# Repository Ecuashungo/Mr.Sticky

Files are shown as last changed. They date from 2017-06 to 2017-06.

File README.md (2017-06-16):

# Mr.Sticky
Mr.Sticky is a robot that has been designed and built in the framework of the STI interdisciplinary robotics competition at EPFL. The working principle of this bottle collecting robot is a sticky conveyor belt that turns around the whole chassis which is used to grab, store and release the bottles.
The data acquisition and its processing is done on board. The bottle detection uses a classifier trained by a Haar cascade using the OpenCV library. The localization of the robot is calculated through a Kalman filter which uses data from encoders and a self-built triangulation system. The latter detects four LED beacons using a camera with a parabolic lens resulting in a panoramic 360 degree view.
This project allowed us to gain experience in time and budget management as well as practical experience such as mechanical design, PCB manufacturing and software programming. 

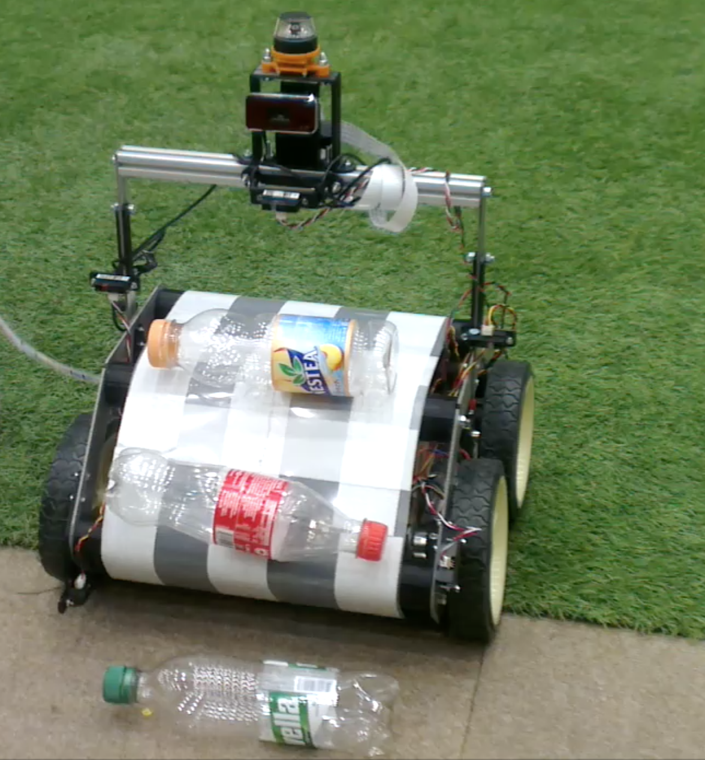
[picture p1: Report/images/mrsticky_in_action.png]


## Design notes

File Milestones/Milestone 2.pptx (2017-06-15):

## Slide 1

STI – robot competition

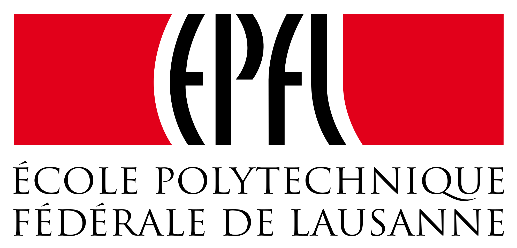
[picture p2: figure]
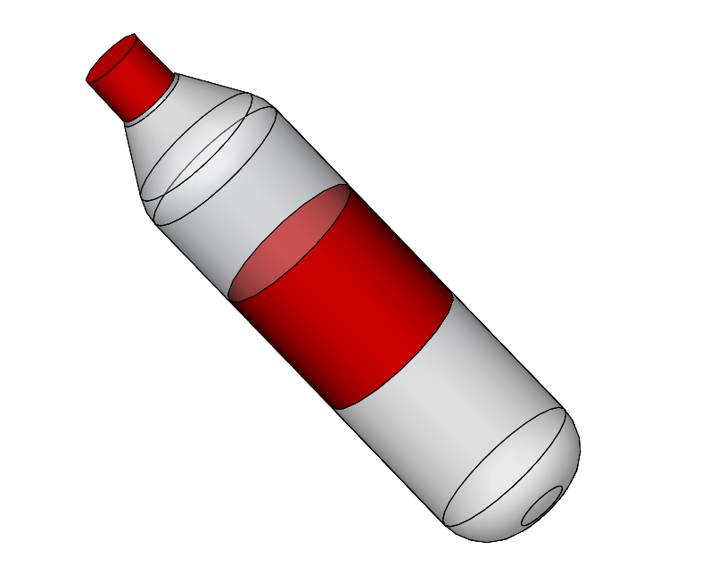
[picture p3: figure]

TEAM 3
Milestone number 2

Claudio Fritsche (GM)
Roman Oechslin (MT)
Héloïse Boross (MT)

20th March 2017

## Functional Analysis

Mechanical Functions | Other Functions
Locomotion | Bottle Detection
Grabbing Mechanism | Obstacle Avoidance
Release Mechanism | Localisation and Navigation
Storage | Time Control
Energy Supply

Research Concept Implementation Risk management

2

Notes: Claudio

## Brainstorming

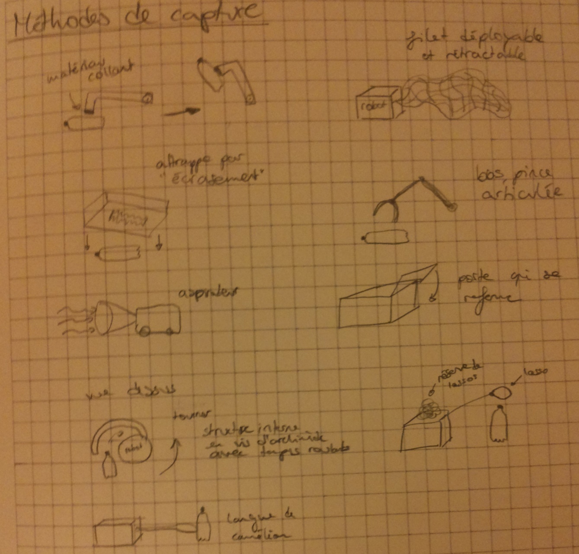
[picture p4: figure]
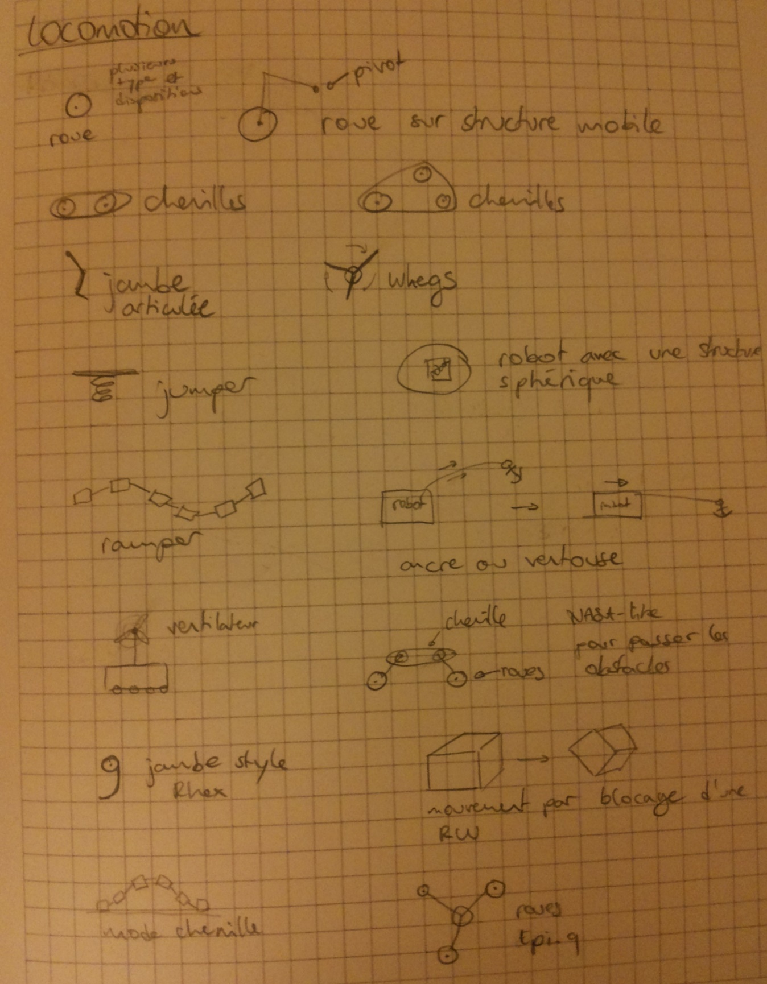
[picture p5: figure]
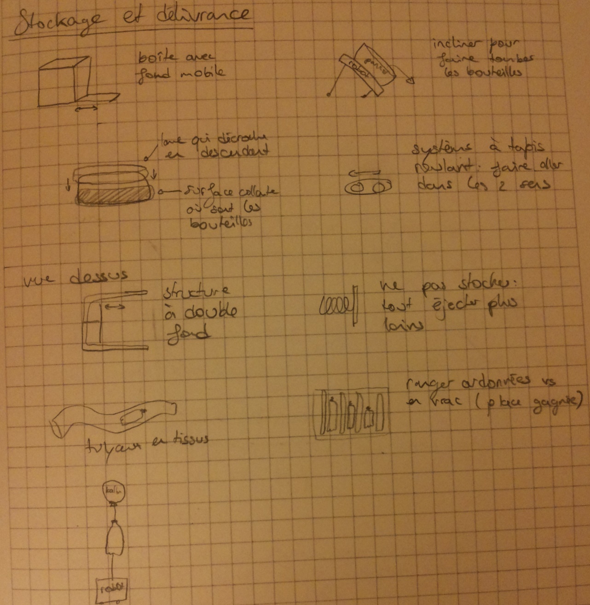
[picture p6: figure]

Research Concept Implementation Risk management

3

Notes: Héloïse

## Robot Design

Grabbing mechanism: sticky conveyor belt

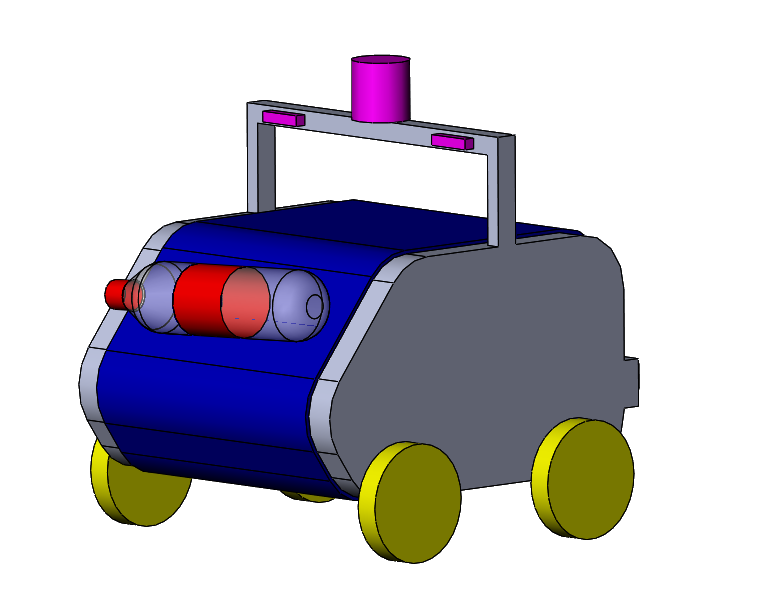
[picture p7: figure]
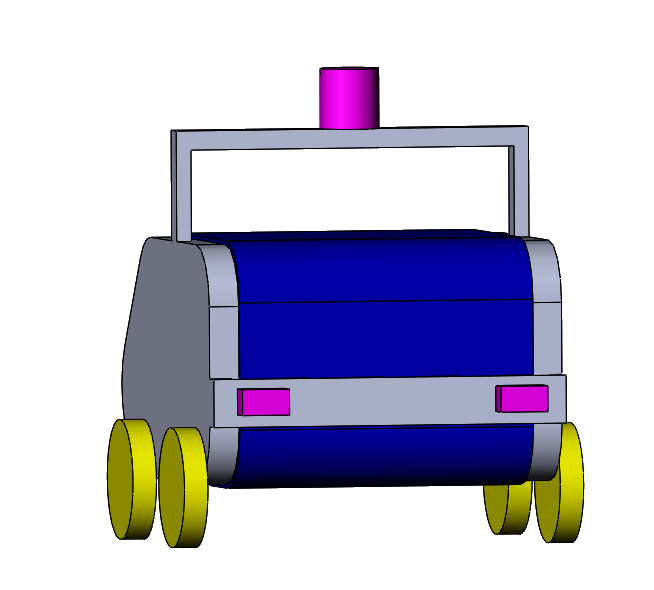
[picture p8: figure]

Bottle releasing mechanism

Navigation and obstacle detection sensors

Calibration sensors

Electronic and battery storage

Locomotion system

Bottle releasing sensor

Research Concept Implementation Risk management

4

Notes: Héloïse
locomotion, grabbing, release —> good explanation
innovative

## Robot Design

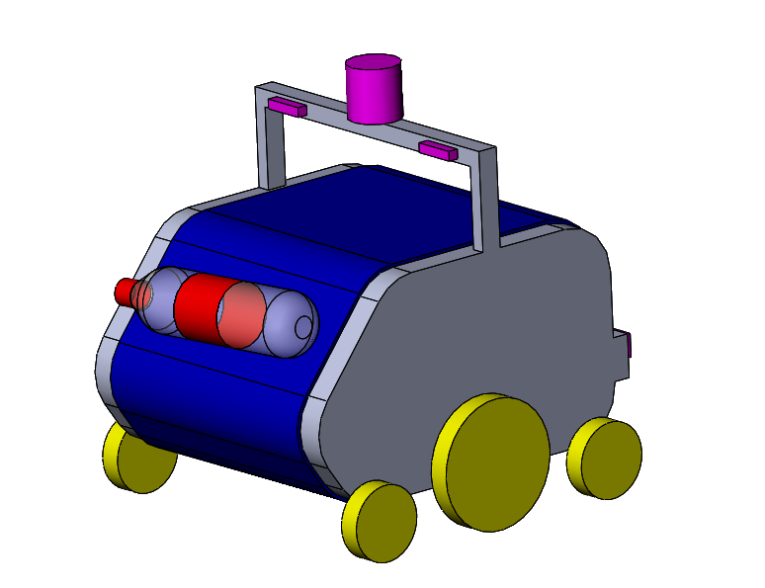
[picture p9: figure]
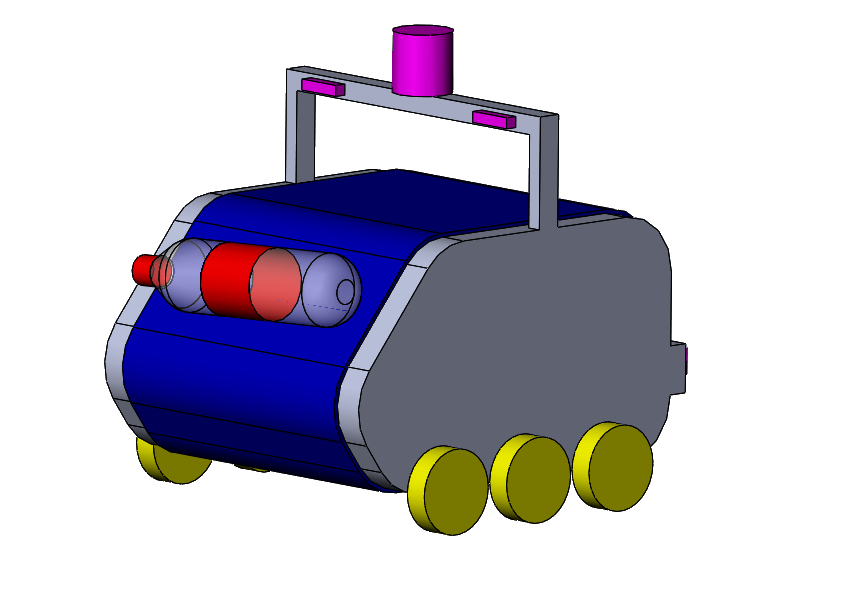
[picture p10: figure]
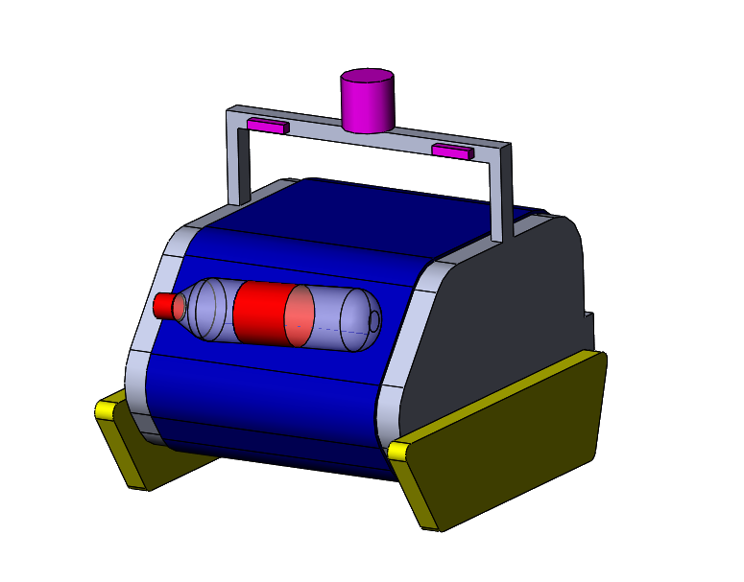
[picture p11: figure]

Research Concept Implementation Risk management

5

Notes: Héloïse
locomotion, grabbing, release —> good explanation

## Parts List

Function | Parts
Locomotion | Chassis | Motors (4x) | Controller (Arduino)
Grab and Release | Conveyor Belt | Sticky Surface | Motor
| Barrier | Light Barrier Sensor | Encoder
Navigation | Encoders (2x) | Camera | Spherical Mirror
| Bumpers (2x)
Bottle Detection | Camera | Raspberry Pi
Obstacle Avoidance | IR-Sensors
Energy Supply | Battery

Research Concept Implementation Risk management

6

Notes: Claudio

Partslist:
Locomotion:
Chassis, Wheels (4x), Motors (4x), Controller (Arduino)

Grabbing + Release:
Conveyor Belt + Sticky surface, 1 Motor (+encoder?), Barrier, Light barrier sensor

Navigation:
encoders (2x or 4x?), camera, spherical mirror

Bottle detection:
Camera, Raspberry Pi with opencv and ROS

Obstacle avoidance:
IR-sensors,

## Open CV

Why OpenCV?
- It’s an open source computer vision library
- Only one sensor (camera) for bottle detection in real time

What? | How? | To Do
Bottle Detection | Haar Cascade | Build Haar Classifier
Navigation | Triangulation with LED’s | Color detection, angle determination
Obstacle Avoidance | Haar Cascade | Build Haar Classifier

Research Concept Implementation Risk management

7

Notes: Claudio

## Navigation

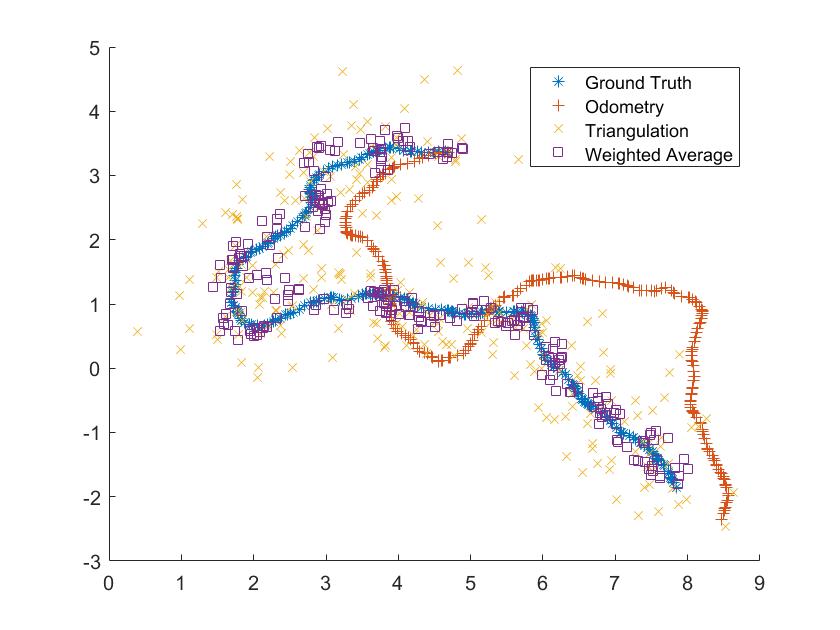
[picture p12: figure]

SLAM / Kalman filter
- Odometry (drift)
- Triangulation (noisy)
- Monocular vision

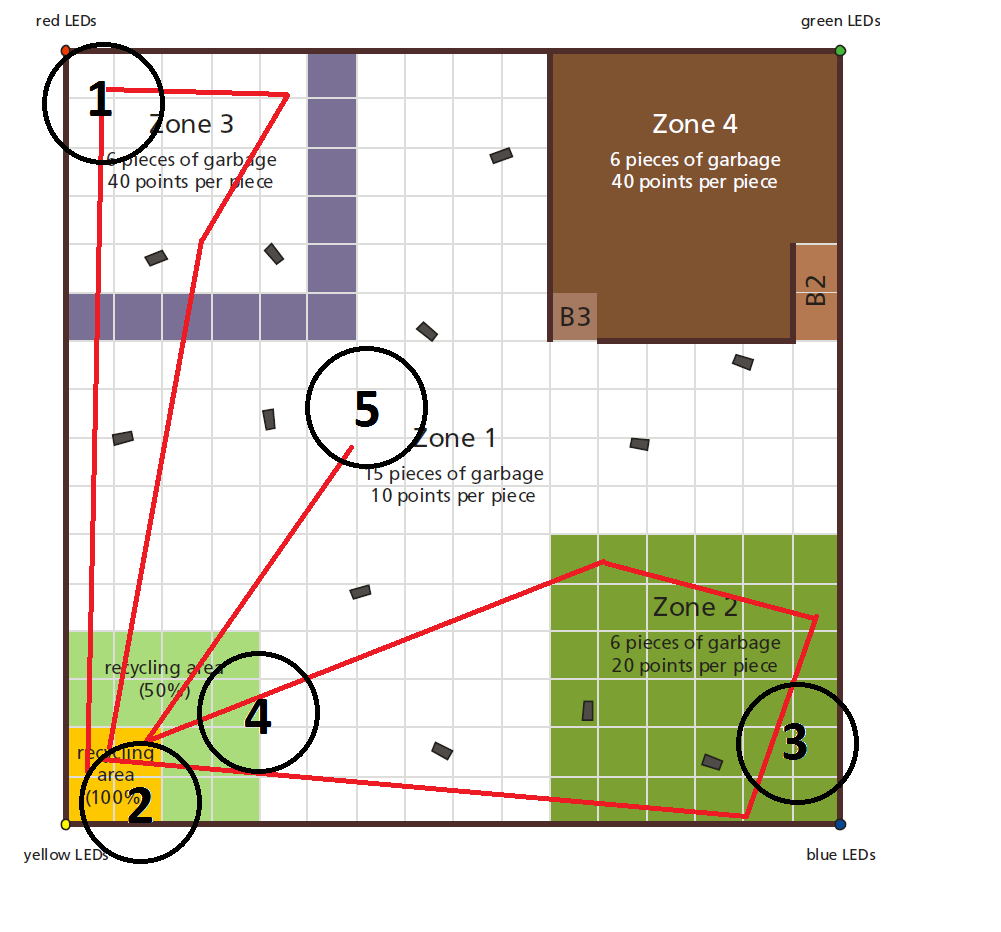
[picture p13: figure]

Research Concept Implementation Risk management

8

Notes: Roman

## Risk analysis

Probability | Problem | Solution
2 | Detection in OpenCV not reliable | Use backup sensors
2 | Navigation doesn’t work | Enough time for testing and improving, at least 2 methods
2 | Conveyor belt doesn’t rotate | Backup plan
3 | Sticky material is not available / damaged / dirty | Backup plan
3 | Malfunctioning of Sensors / Motors | Buy enough / Redundancy
4 | Get stuck on stones | Bigger wheels, tank treads
4 | No time for testing robot | Webots
5 | Don’t know orientation of bottles on conveyor belt | Light barrier

1: Low
5: High

Research Concept Implementation Risk management

9

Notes: Roman

## Back-up plan

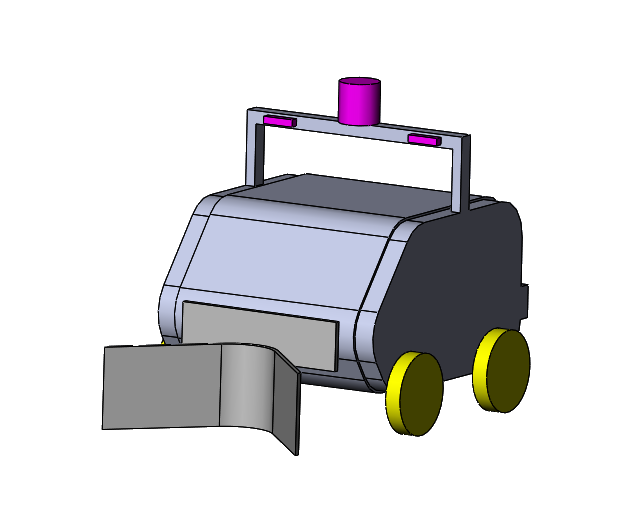
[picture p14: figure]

Research Concept Implementation Risk management

10

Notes: Roman

## Time Management

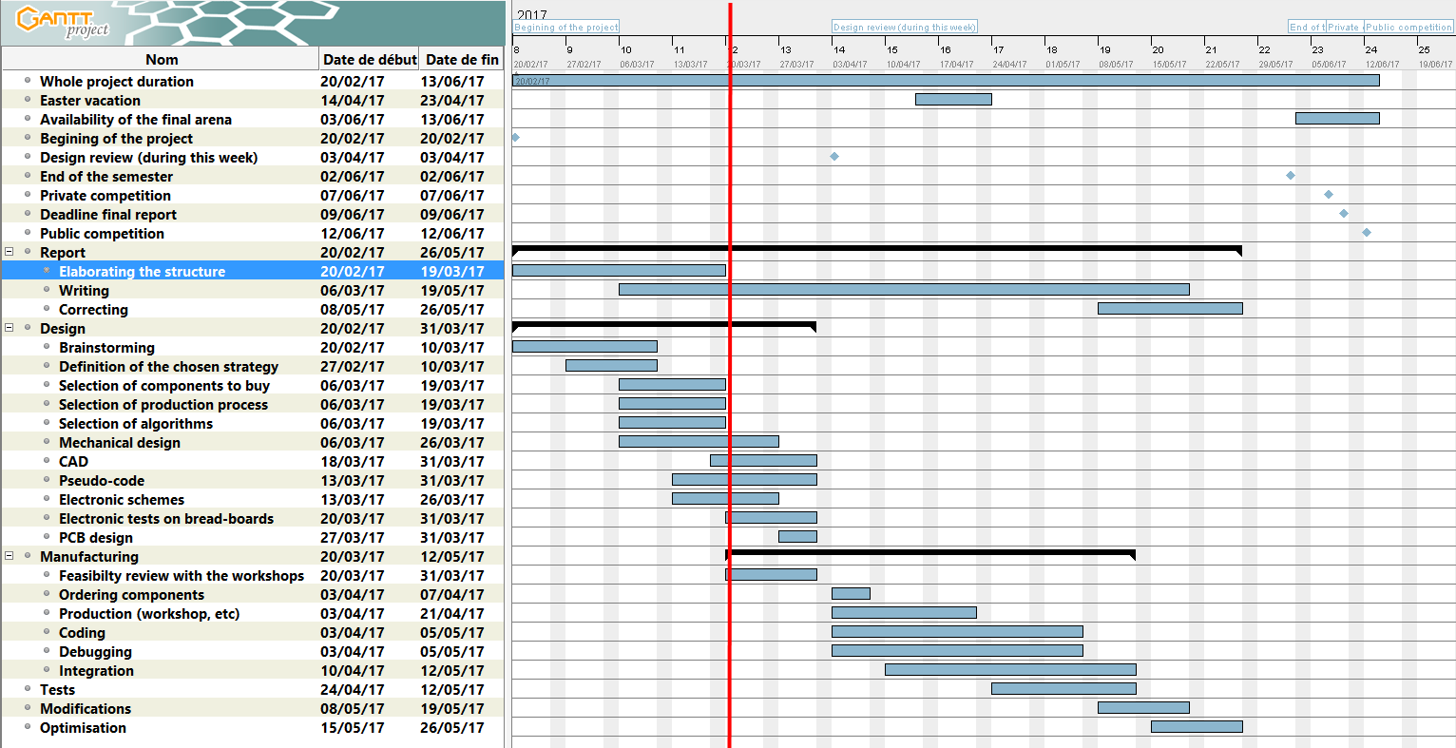
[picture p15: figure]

Research Concept Implementation Risk management

11

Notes: Roman

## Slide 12

Thank you for your attention

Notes: Questions?

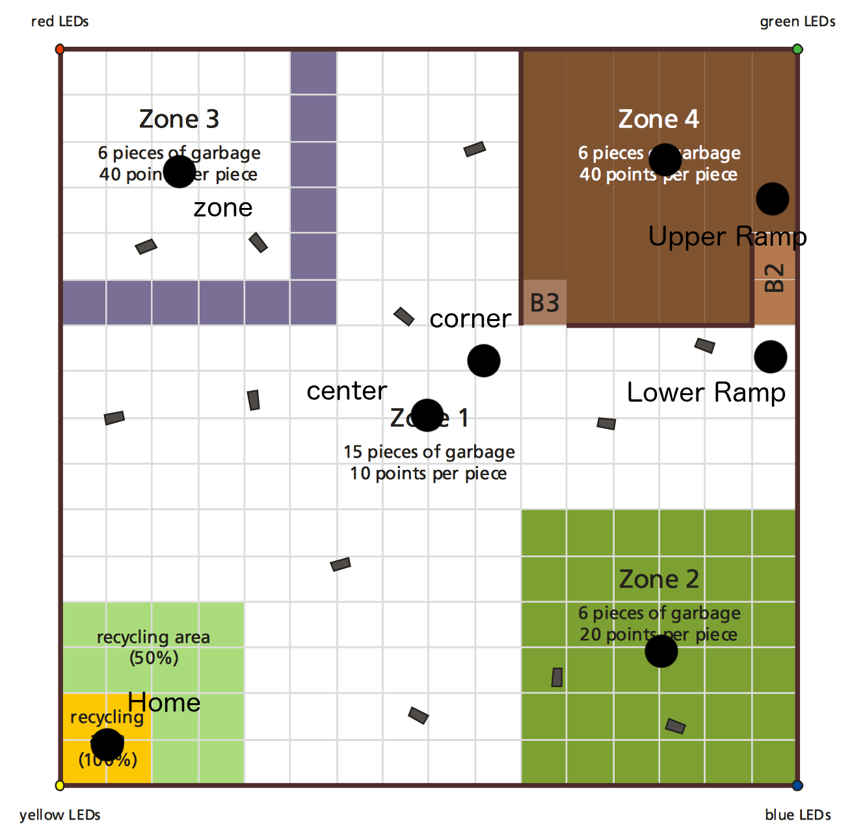
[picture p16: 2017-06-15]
Report/images/arena_waypoints.png

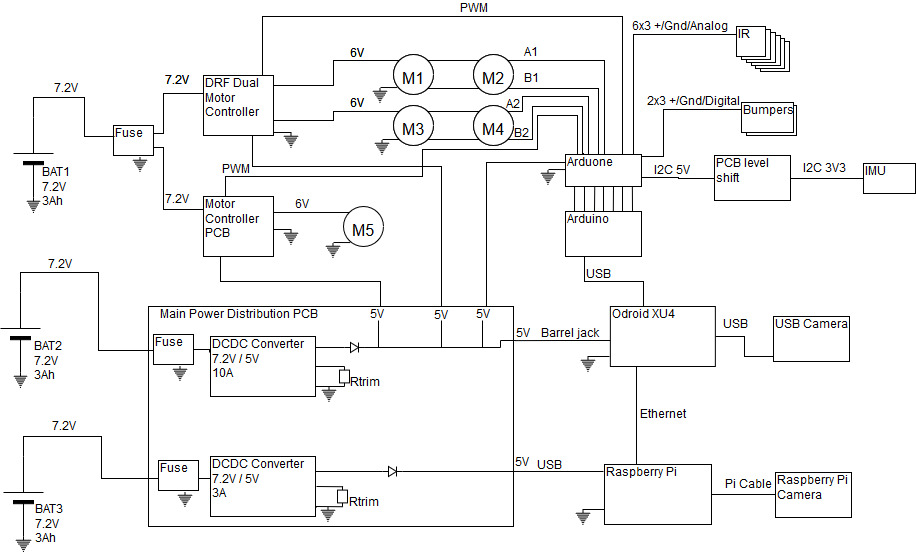
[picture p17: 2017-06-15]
Hardware/Electrical Schematic_no_grnd.jpg

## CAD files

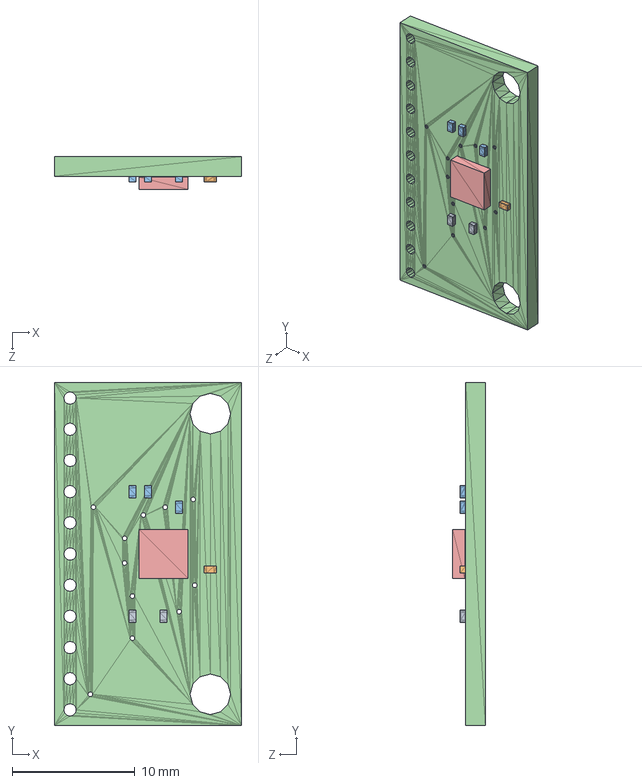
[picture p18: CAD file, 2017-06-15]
Hardware/AltiumDesigner/Imu_level_shift/IMU.step
15.2 x 27.9 x 2.67 mm

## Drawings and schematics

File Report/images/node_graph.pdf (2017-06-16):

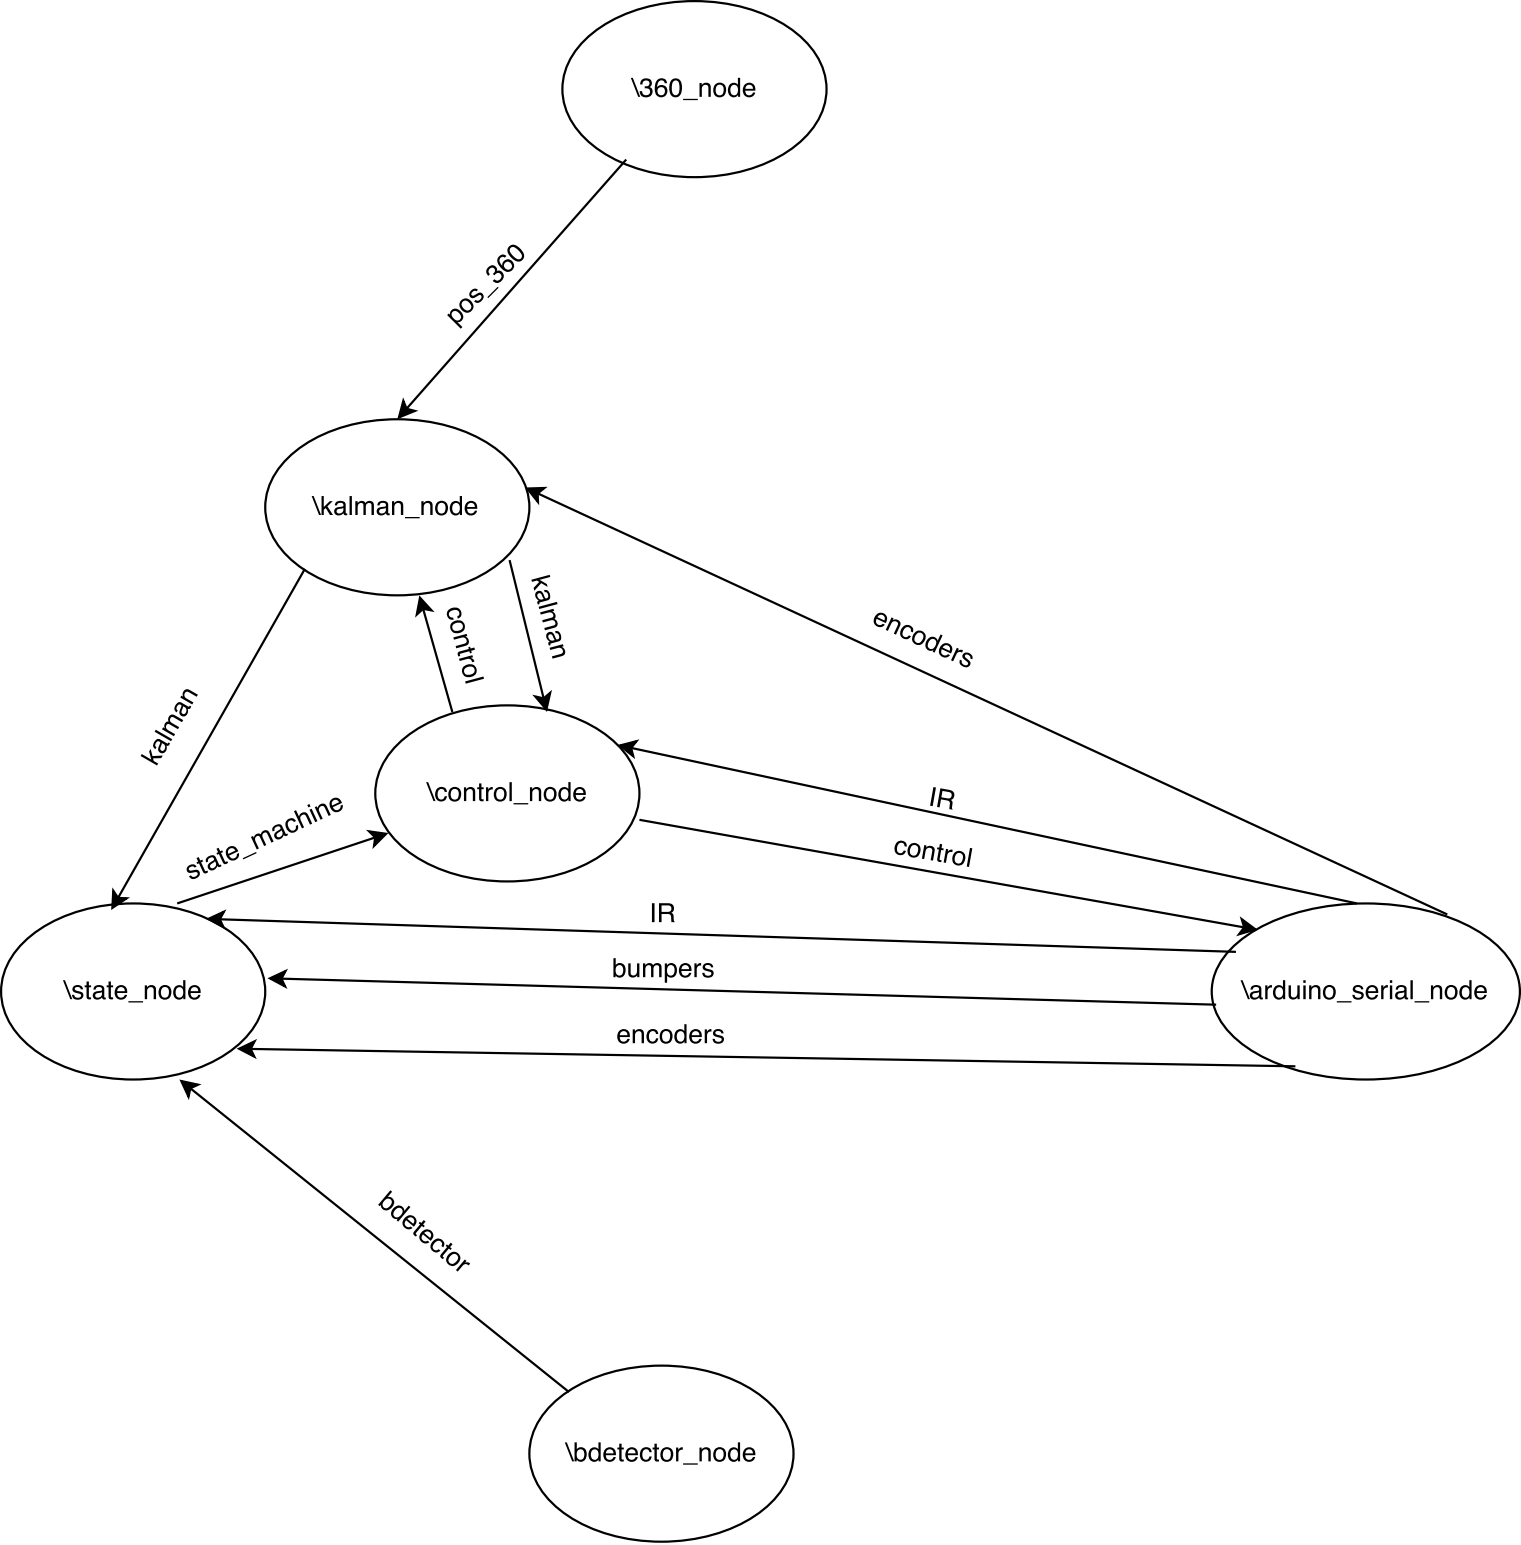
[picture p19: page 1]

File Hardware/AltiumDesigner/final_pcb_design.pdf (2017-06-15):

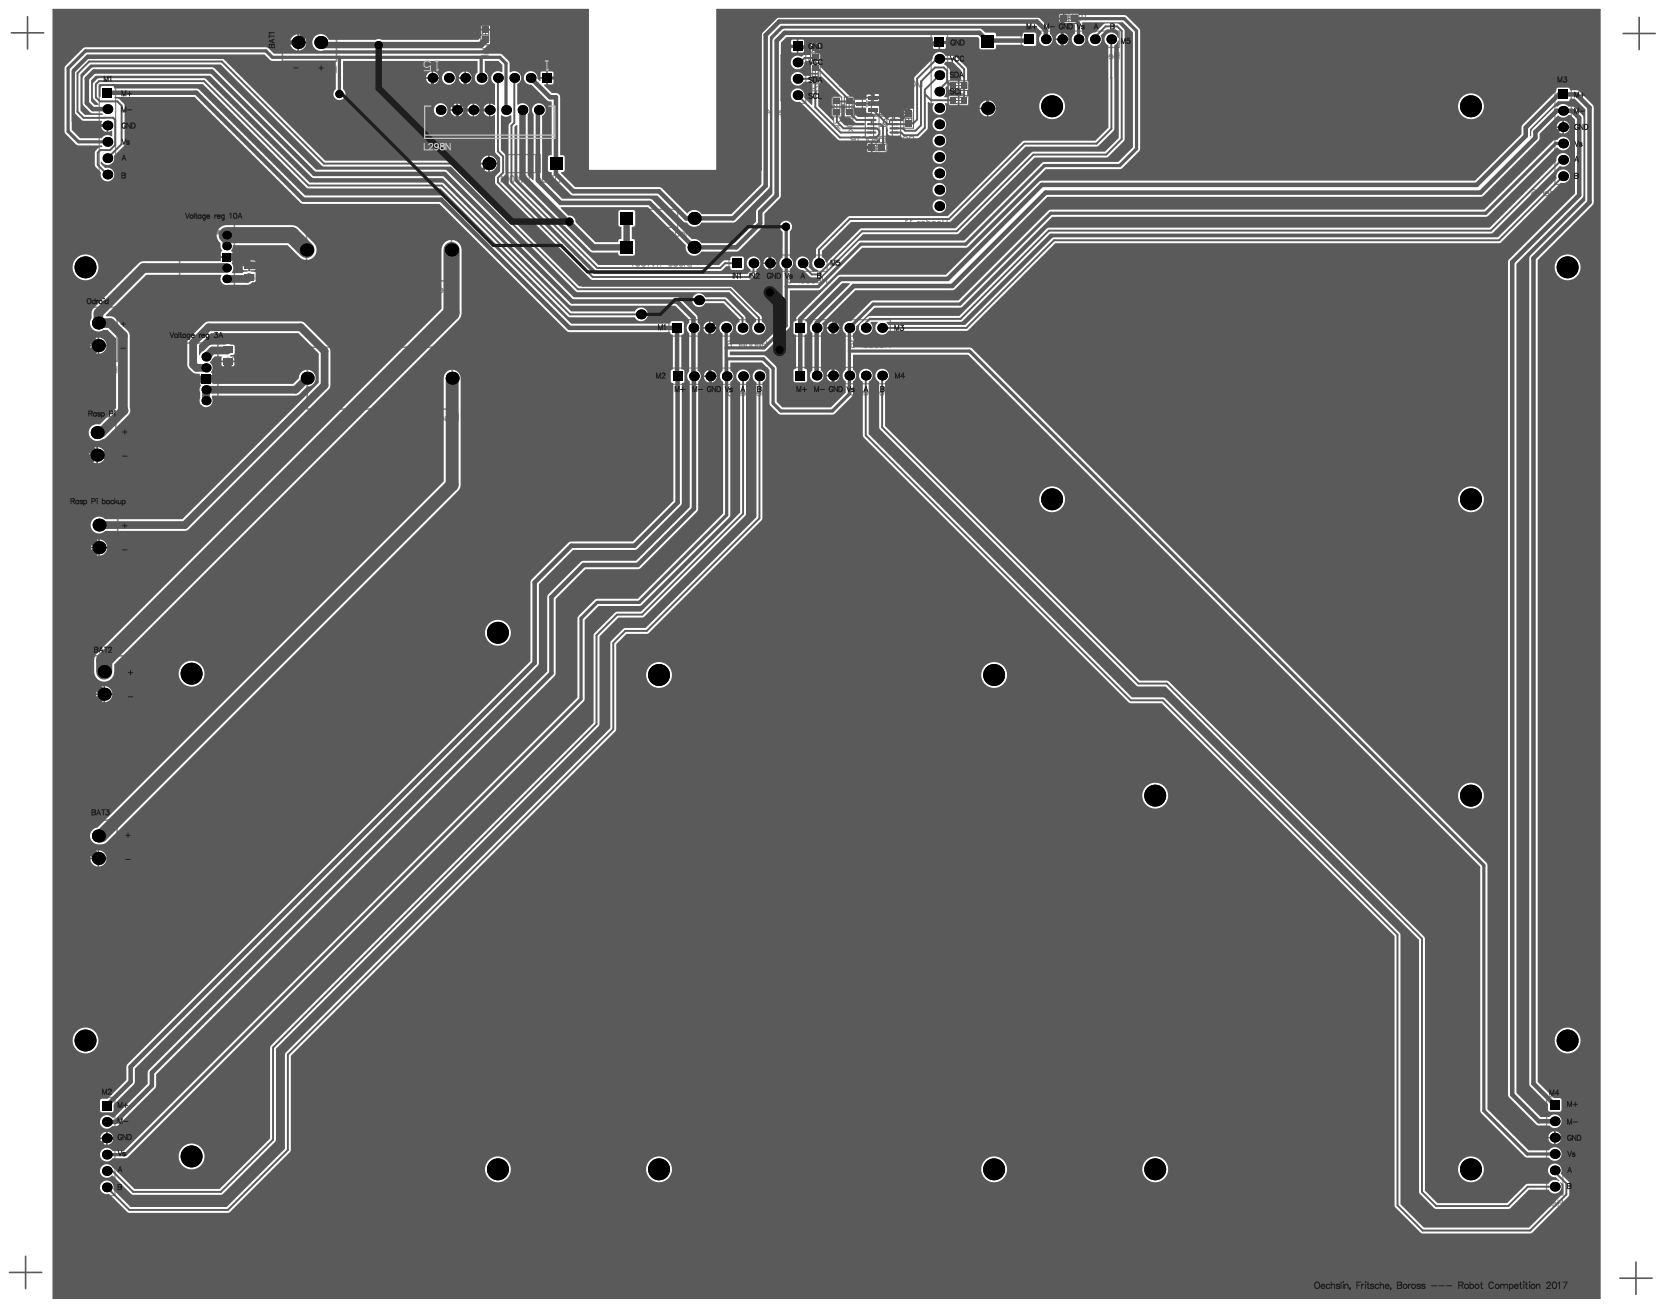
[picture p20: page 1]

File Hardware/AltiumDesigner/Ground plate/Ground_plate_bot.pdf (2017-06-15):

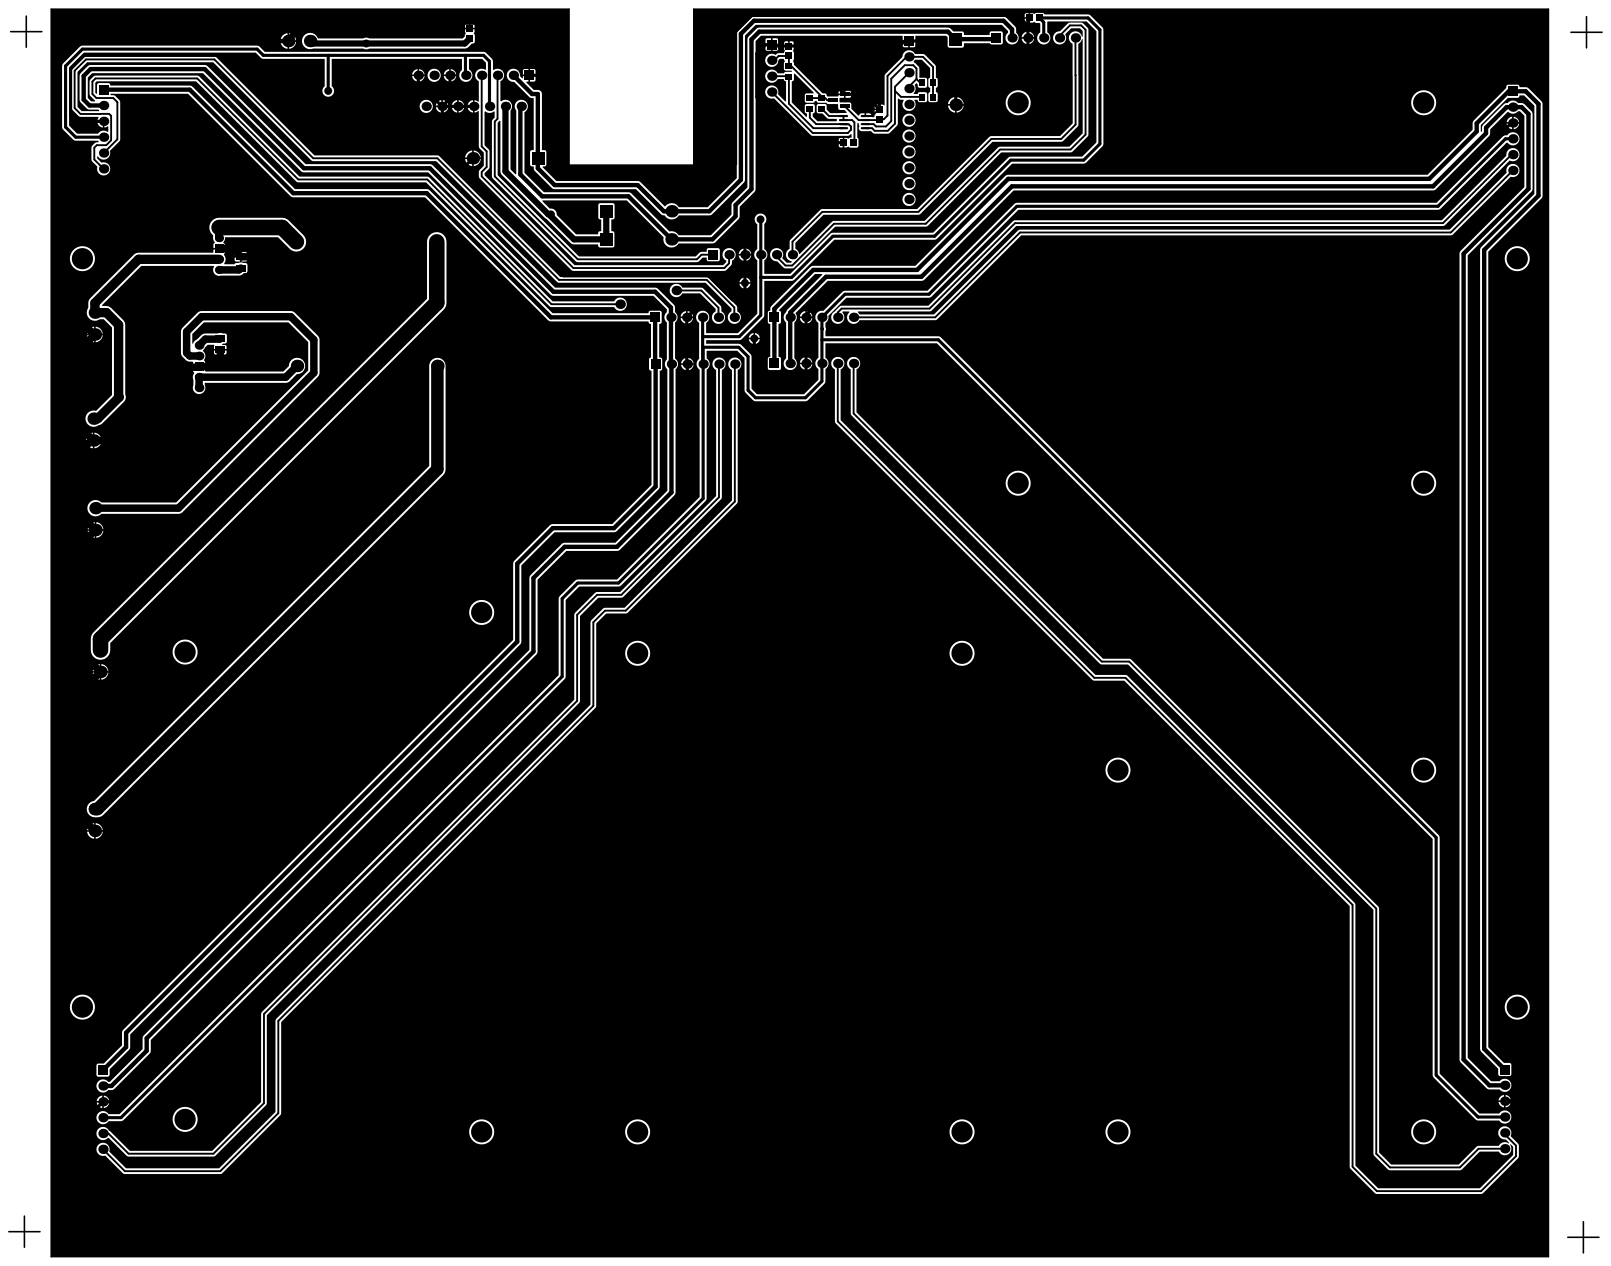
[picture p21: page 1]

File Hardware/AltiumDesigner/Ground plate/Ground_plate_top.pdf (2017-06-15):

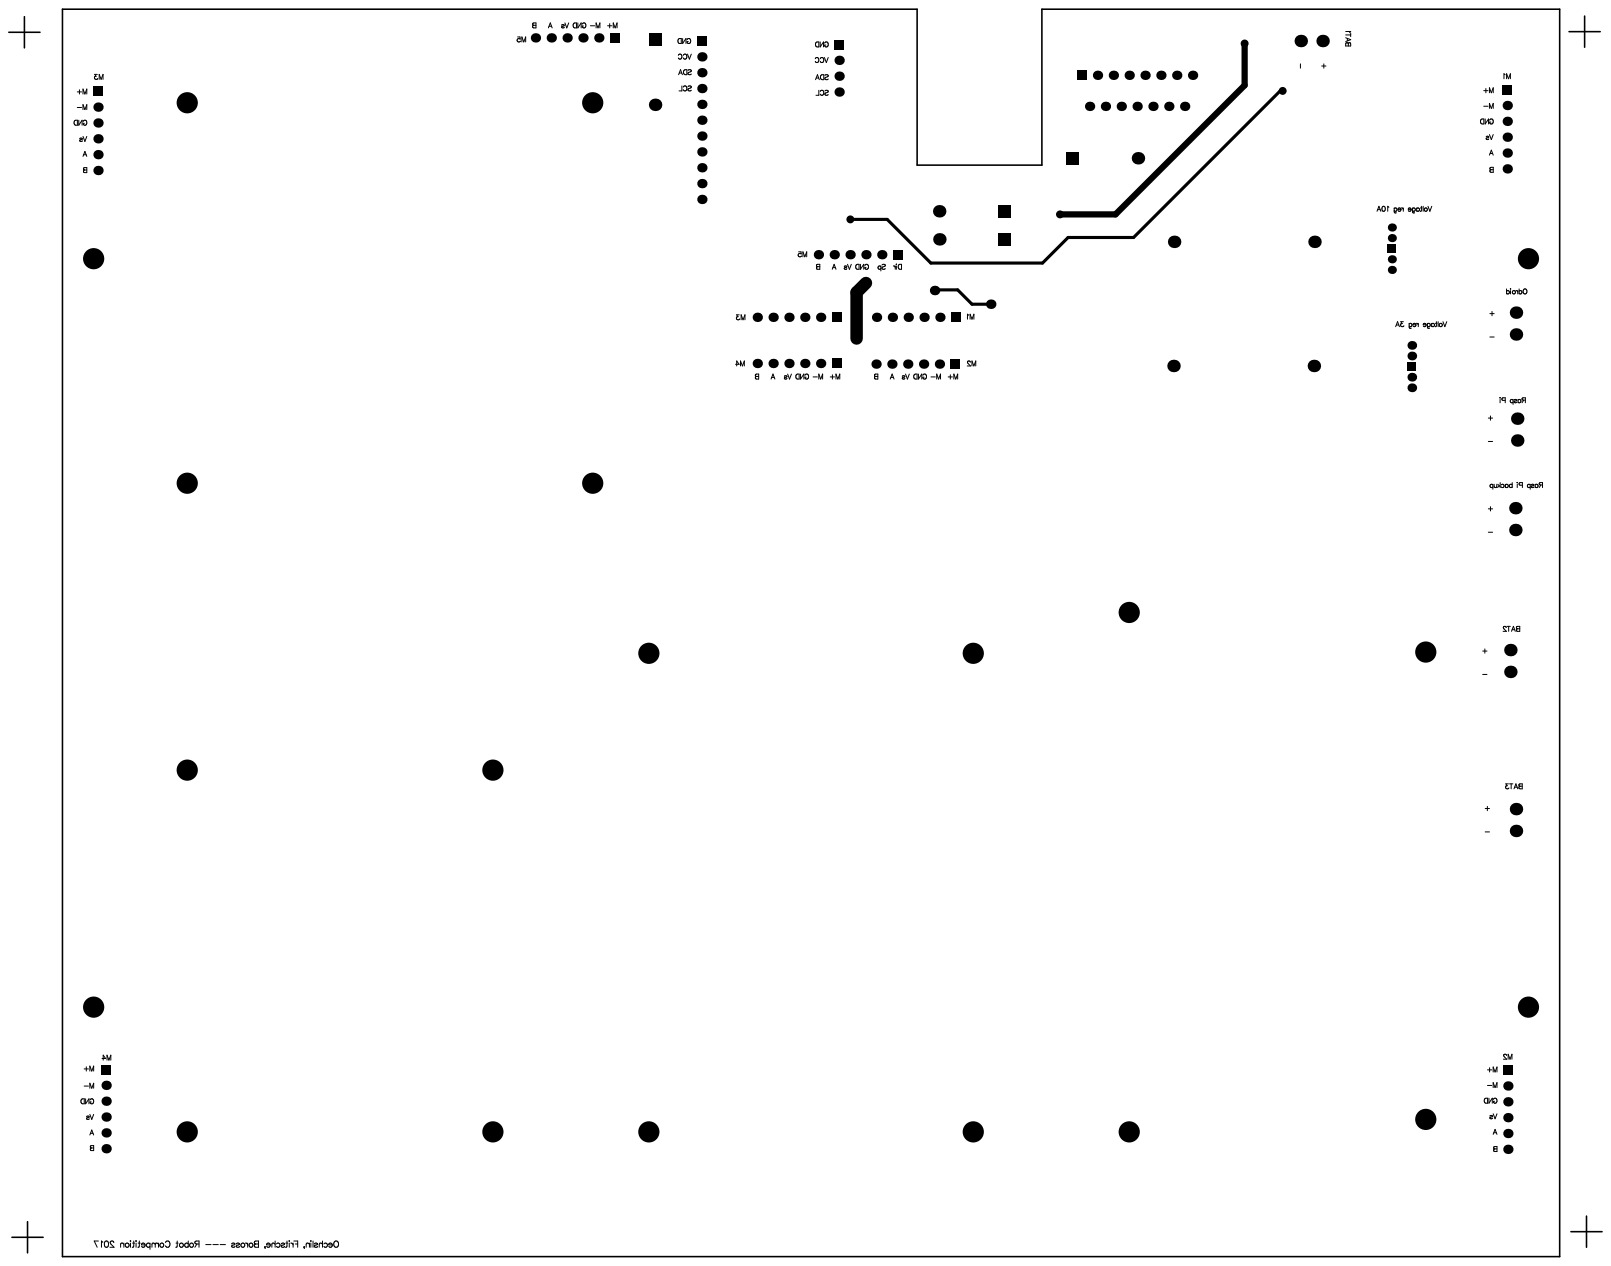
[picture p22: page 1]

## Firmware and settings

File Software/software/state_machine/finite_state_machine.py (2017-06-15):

import numpy as np
import sys
sys.path.append("/home/odroid/sticky-robot/software/parameters/")
import parameters as param
import math
import rospy

# Define constants
DEBUG = param.get_debug_verbose() # can be zero or one for debugging purposes
CV_LOAD = 1
CV_UNLOAD = -1
CV_REST = 0
NO = 0

# Define coordinates for the stage and home
STAGE_X = 5  # [m] x coord where the stage begins
STAGE_Y = 6  # [m] y coord where the stage begins
HOME_XY = 2  # [m] coords for the home base
ARENA_LIMIT_MAX = 7.8  # [m] define the maximum of the arena
ARENA_LIMIT_MIN = 0.2

class State_pose:
    def __init__(self, name, pos=[0., 0., 0., 0., 0.]):
        self.name = name
        self.x = pos[0]  # [m]
        self.y = pos[1]  # [m]
        self.theta = pos[2]  # [rad]
        self.conv_direction = pos[3]
        return

    def update(self, pos):
        self.x = float(pos[0])
        self.y = float(pos[1])
        self.theta = float(pos[2])
        self.conv_direction = float(pos[3])
        return np.array([self.x, self.y, self.theta])

    def get_state_pose(self):
        return [self.x, self.y, self.theta, self.conv_direction]

    def get_state_pose_as_vec(self):
        return np.array([[self.x], [self.y], [self.theta], [self.conv_direction]])


class State_machine():
    def __init__(self):
        # Waypoints: zone_1 = center, zone_2 = grass, zone_3 = stones, zone_4 = stage
        self.way_points= {"home": [0.5, 0.5, 0], "zone_1": [4, 4, 0], "zone_2": [4, 1, 0],
                          "zone_3": [1.5, 6.5, 0], "corner": [4.5, 5.5, 0], "before_ramp": [7.75, 5, math.pi/2],
                          "after_ramp": [7.75, 7.5, math.pi/2], "zone_4": [6.5, 7, -math.pi]}
        # list of goals that want to be reached
        self.goal_list = []
        self.goal_list.append(self.way_points['zone_1'])
        self.goal_list.append(self.way_points['zone_3'])
        self.goal_list.append(self.way_points['zone_2'])

        # Define intiial state
        self.state = "init"
        self.initial_time = None  # is None until game starts
        self.my_pose = State_pose("state_pose")
        self.my_pose.x = self.way_points['home'][0]
        self.my_pose.y = self.way_points['home'][1]
        self.my_pose.theta = self.way_points['home'][2]

        # define variables updated by bdetector
        self.x_angle_to_bottle = 0
        self.y_angle_to_bottle = 0
        self.bottle_found = False  # boolean value
        # this is the angle permitting to go off the route and collect a bottle
        self.bottle_angle_allowance = math.pi
        self.amount_of_bottle_grab_trials  = 0  # says how many times we have tried to grab a bottle until homing

        self.hunting = False  # indicates if a bottle has been found that we want to get
        self.started_grabbing = False  # indicates whether a grabbing has already been started
        self.started_loading = False  # indicates whether loading has started
        self.releasing = False  # indicates whether we want to release the bottles (only in recycling area)
        self.loading = True  # indicates if we want to load or unload
        self.l_encoder_before_grabbing = 0  # [m] temp value to save encoder distance
        self.r_encoder_before_grabbing = 0
        self.c_encoder_before_turning = 0
        self.i_am_stuck = 0  # counter that indicates if we have spent too much time on the same spot
        self.goal_update_time = None

        # bottle approach variables
        self.loading_time = None
        self.temp_bottle_approach_pos_x = None  # State_pose("temp_bottle")
        self.temp_bottle_approach_pos_y = None

        # initialize readings for ir sensors
        self.ir_front = 0  # is an arbitrary number, somehow related to distance, thresholds are given in param file
        self.ir_left = 0
        self.ir_center = 0
        self.ir_right = 0
        self.ir_back = 0
        self.ir_bottom = 0  # detects if bottle is in front of us

        # initialize bumper readings
        self.bumper_left = False  # says if bumper is pressed
        self.bumper_right = False

        # initialize readings for encoders
        self.l_encoder_dist = 0.0  # [m] distance covered according to encoders
        self.r_encoder_dist = 0.0
        self.c_encoder_dist = 0.0
        return

    # function that checks if the goal corresponds to the actual position given by kalman
    def are_we_there(self, goal):
        THRESHOLD = param.get_arrival_threshold()
        ANGLE_THRESHOLD = param.get_arrival_angle_threshold()
        if (goal.x - self.my_pose.x) < THRESHOLD:
            if (goal.y - self.my_pose.y) < THRESHOLD:
                if (goal.theta - self.my_pose.theta) < ANGLE_THRESHOLD:
                    return True
        else:
            return False
        return

    # this function projects a bottle based on the detected angle this is necessary since it is not known how far the
    # the bottle actually is
    def create_goal_from_bottle(self):
        x_angle = self.x_angle_to_bottle
        theta = self.my_pose.theta

        dist = param.get_distance_of_virtual_bottle_fsm() # [m] distance for next goal
        x_goal = self.my_pose.x + dist * math.cos(x_angle + theta)
        y_goal = self.my_pose.y + dist * math.sin(x_angle + theta)
        theta_goal = self.limit_angle_to_2pi(self.my_pose.theta + x_angle)
        self.goal_list.append([x_goal, y_goal, theta_goal])
        #return self.goal_list[-1]
        return [x_goal, y_goal, theta_goal]

    # this obstacle avoidance is used to smooth out the way and create a new goal
    # there is a second obstacle avoidance implemented in control
    def avoid_obstacles(self, goal):
        # define rotating angle alpha
        alpha = param.get_alpha_for_obstacle_avoid_fsm()  # [rad] the angle that is used to rotate the goal
        coeff = param.get_factor_for_obstacle_avoid_fsm()  # multiplying factor if obstacle in center

        left_blocked = self.ir_left > param.get_ir_left_threshold_fsm()
        center_blocked = self.ir_center > param.get_ir_center_threshold_fsm()
        right_blocked = self.ir_right > param.get_ir_right_threshold_fsm()
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

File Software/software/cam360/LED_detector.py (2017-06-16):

import cv2
from picamera.array import PiRGBArray
from picamera import PiCamera
import numpy as np
import time
import math as m
from random import getrandbits
import os

import LED as l
import triangulation as tri


## FUNCTIONS:

def visualize(image_list):
    """
    This function works
    :param image_list: list with images to be visualized
    :return: 
    """
    if not isinstance(image_list, list):
        image_list = [image_list]

    while True:
        i = 0  # for the names of the windows
        for img in image_list:
            cv2.imshow(str(i), img)
            i = i + 1
        if cv2.waitKey(1) & 0xFF == ord('q'):
            print('quit successfully \n')
            break
    cv2.destroyAllWindows()

def morph(image, kernel_size, mode):
    """
    makes opening or closing
    :param img: 
    :param kernel_size: 
    :param mode: either "oc": opening then closing
                        "dod": dilate, open and dilate
    :return: 
    """
    img = image
    kernel = np.ones((kernel_size, kernel_size), np.uint8)

    if mode == 'oc':
        opening = cv2.morphologyEx(img, cv2.MORPH_OPEN, kernel)
        closing = cv2.morphologyEx(opening, cv2.MORPH_CLOSE, kernel)
        ret = closing

    elif mode == 'dod':
        dilate = cv2.dilate(img, kernel, iterations=1)
        opening = cv2.morphologyEx(dilate, cv2.MORPH_OPEN, kernel)
        dilate2 = cv2.dilate(opening, kernel, iterations=1)
        ret = dilate2

    elif mode == 'dodd':
        dilate = cv2.dilate(img, kernel, iterations=1)
        opening = cv2.morphologyEx(dilate, cv2.MORPH_OPEN, kernel)
        dilate2 = cv2.dilate(opening, np.ones((kernel_size + 1, kernel_size + 1), np.uint8), iterations=1)
        ret = dilate2

    elif mode == 'nothing':
        ret = img

    return ret

def triangulation(led_list):
    triang = tri.Triangulation(led_list)
    pos = triang.run()
    return pos

def auto_canny(image, sigma=0.33):
    """
    Function that calculates a canny edge detection with quite good parameters
    :param image: 
    :param sigma: 
    :return: 
    """
    # compute the median of the single channel pixel intensities
    v = np.median(image)

    # apply automatic Canny edge detection using the computed median
    lower = int(max(0, (1.0 - sigma) * v))
    upper = int(min(255, (1.0 + sigma) * v))
    edged = cv2.Canny(image, lower, upper)

    # return the edged image
    return edged

class LEDDetector:
    """
    This class starts the color detector and creates LED objects, calculates the angles between the leds and finally 
    calculates the position and orientation of the robot through the triangulation funciton.

    """

    # todo-cf: solve problems, see above
    def __init__(self):
        # self.color = color

        # predefined ranges for 4 colors
        # todo-cf: update these color values wit LED-Tests!
        self.color_dict = {"blue_low": np.array([100, 120, 200]), "blue_high": np.array([130, 255, 255]),
                           "yellow_low": np.array([10, 0, 150]), "yellow_high": np.array([60, 40, 255]),
                           "green_low": np.array([65, 120, 86]), "green_high": np.array([90, 255, 255]),  # was 90-130
                           "red_low": np.array([160, 100, 100]), "red_high": np.array([200, 255, 255])}

        self.color_print_dict = {"blue": (176, 0, 0), "yellow": (42, 208, 255),
                                 "green": (42, 173, 255), "red": (51, 62, 255)}

        # dictionary containing all settings
        self.config_dict = {}

        # robot position variables
        # todo-cf: add romans class
        self.position = [None, None, None]  # [x, y, theta]

        # led position variables
        self.pos_reference = []

        # LED's
        self.yellow = l.LED("yellow")
        self.blue = l.LED("blue")
        self.green = l.LED("green")
        self.red = l.LED("red")
        self.led_list = [self.yellow, self.blue, self.green, self.red]
        self.angle_list = [self.yellow.angle, self.blue.angle, self.green.angle, self.red.angle]

        # video capture
        self.cap = None
        self.frame = None
        self.gray = None
        self.hsv = None
        self.ret = None
        self.windowsize = [0, 0]
        self.bool_video = False

        # initialize video variables
        self.output_mask = None

        # visualisation
        self.bool_visualisation = False
        self.bool_debug_vis = False

        # information of circular ROI
        # todo-cf: maybe implement initialization function with hough circle transform
        self.radius = int(self.windowsize[0] * 0.25)
        self.camera_center = [0, 0]

        # init picamera
        self.camera = None
        self.rawCapture = None
        
        self.counter = 0
        print('Initialization done')

    def init_cam(self, visualisation=False, verbose=False):
        # todo-cf: test individually
        self.camera = PiCamera()
        self.camera.resolution = (1080, 960)

        self.rawCapture = PiRGBArray(self.camera)
        self.windowsize = [self.camera.resolution[1], self.camera.resolution[0]]
        if verbose:
            print("self.windowsize: ", self.windowsize)
        self.radius = int(self.windowsize[0] * 0.25)
        self.output_mask = np.zeros((self.windowsize[0], self.windowsize[1]), np.uint8)
        time.sleep(0.1)
        self.camera.capture(self.rawCapture, format="bgr")
        self.frame = self.rawCapture.array
        if verbose:
            print("self.windowsize: ", self.windowsize)
            print("shape frame after rawCapture.array", self.frame.shape)
        self.rawCapture.truncate(0)
        self.truncate(visualisation=visualisation, verbose=verbose)
        if visualisation:
            print("self.frame before flip")
            visualize(self.frame)
        self.flip()
        if visualisation:
            print("self.frame after flip")
            visualize(self.frame)

    def get_frame(self, verbose=False, visualisation=False):
        # todo-cf: test individually
        self.camera.capture(self.rawCapture, format="bgr")
        self.frame = self.rawCapture.array
        self.gray = cv2.cvtColor(self.frame, cv2.COLOR_BGR2GRAY)
        self.windowsize = list(self.frame.shape[0:2])
        if visualisation:
            print('self.frame after reading from picam: ')
            visualize([self.frame])
        if verbose:
            if self.frame is None:
                print('self.frame is None')

        # truncate manually for right roi
        self.truncate(verbose=verbose, visualisation=visualisation)
        self.flip()

        self.rawCapture.truncate(0)

    def color_mask(self, visualisation=False):
        """
        This method creates the colormasks of the leds in self.led_list 
        :return: 
        """
        img = self.frame
        self.hsv = cv2.cvtColor(img, cv2.COLOR_BGR2HSV)
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

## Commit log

2017-06-15 add datasheets and milestones and altium designer
    [Ale.PcbLib, Ale.SchLib, DCDC_converters.PcbDoc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]
2017-06-16 create arduino script in dedicated folder
